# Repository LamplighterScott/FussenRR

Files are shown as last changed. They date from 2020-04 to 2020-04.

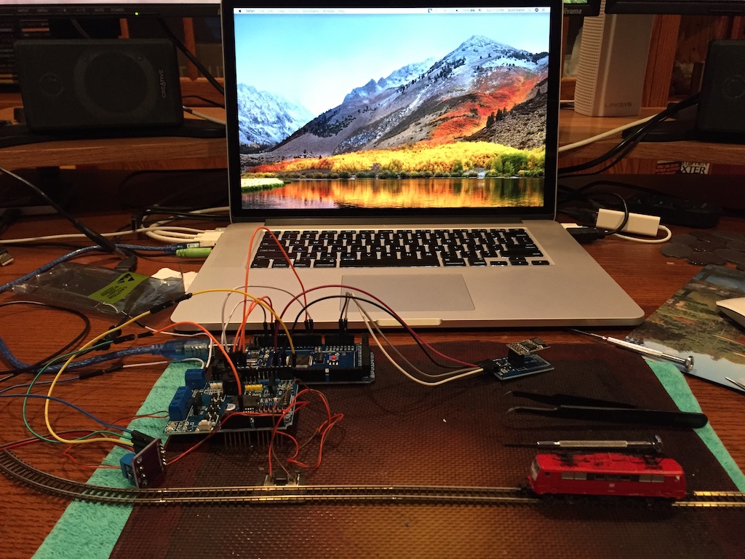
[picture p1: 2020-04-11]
IMG_0338 - Initial Testing.JPG

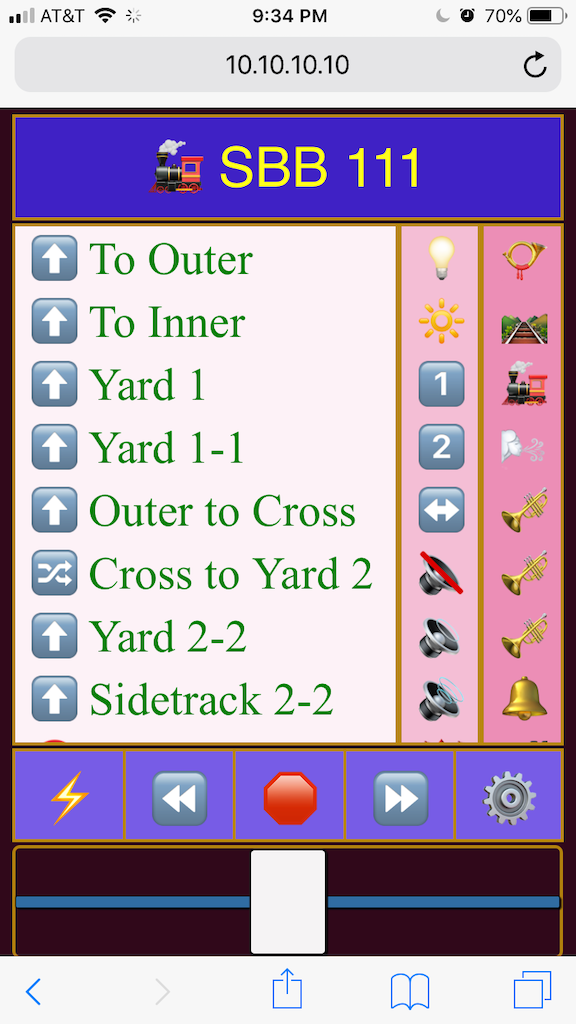
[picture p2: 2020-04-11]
IMG_1388 - Safari Controller.png

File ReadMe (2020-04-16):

FussenRR is a battery-operated Marklin Z model train set designed as a center piece for a dining room table.
It is completely controlled by a smart phone except for power on/off.  The name is taken from the train station
near Neuschwanstein castle in Germany.

It runs on a TalentCell Power Bank YB12011000-USB rechargeable battery (11,000 mAh), Geekcreit "Arduino Mega",
DeekRobot Motor Shield, Espressif ESP-01, Open-Smart ESP-01 Uart adapter, DF Player Mini, DSN-Mini-360 voltage
regulator (5v in 4.2v out), seven FLAMIN Robot 4 UO1 MOSFET relays, four TI 74HC595N shift registers.

The TalentCell lasts a long time inbetween charges.  It has three outputs.  The 12v output supplies the MOSFET
relays controlling eight turnouts (two solenoids each), four decouplers (one solenoid each) and one signal (two solenoids),
as well as some structure LED lights.  The 9v output supplies the motor shield for the DCC signal to the tracks and engines.
The 5v output supplies 1) the ESP-01/Adapter, 2) DF Mini Player/voltage regulator, 3) the shift
registers/turnout LEDs and 4) some LED structure lights.

The Motor Shield is piggy backed on the Mega and includes one jumper from pin 2 to 13 to configure it for DDC.
It is receives 12v from the battery.  It supplies power to the Mega and puts out the DCC signal to the main and
engine programming tracks.

The Mega operates on the 9v from the Motor Shield or five volts from the USB connection to a PC.
Serial zero is reserved for communication to a PC for script loading, debugging and engine programming via JMRI.
Serial one is for the DF Player.  Serial three is for the ESP-01.  Pinouts 2-13 (not all) are reserved for the Motor Shield.
Analog A0 and A1 pinouts measure the Motor Shield output amperage, allowing the Mega to disable the track power output
in case of a short on the tracks.  Turnouts, decouplers and signals are controlled by pinouts 22 to 49.  In order to
function as the DCC++ controller, talk to the ESP-01, DF Player, shirt registers and MOSFETs, you need to upload the
"DCCpp_Mega_MZ.ino" Arduino script to the Mega.  The upload speed is set in the script at 115,200 baud.  Make sure your
IDE (Arduino, ATOM, etc.) has the required library download to it from github, DFRobotDFPlayerMini).  The upload is carried
out on Serial Zero Tx0/Rx0 which can be accessed via the Mega's USB port from a PC.  The Mega has build-in USB to Uart
converter for this purpose.

The MOSFET circuits receive individual high signals from the Mega pin outs 22-49.  One MOSFET drives one solenoid.
Switching is via the negative outputs.  Positive is common.

The shift registers receive clock and data signals from three Mega pin outs (A13, A14, A15).  They drive all the turnout LEDs.
A series of resisters drop the voltage on the positive to each of the red and green LEDs so the brightness is
consistent between the two colors and the rest of the lighting on the set.  Switching is by the positve outputs.
Negative is common.

The DF Player is connected to the Mega's Serial One Tx1/Rx1 pins with a 1k ohm resister between the Mega's Tx1 pi
and the DF Player's Rx pin in order to drop the voltage from 5v to 3.3v.
The DF Player removable flash card is loaded with mp3 sound files.  Each MP3 file name must start with four digits.
The numbers should be in a continuous sequence: 0001xxx.mp3, 0002yyy.mp3 ... 0024zzz.mp3.
xxx, yyy and zzz can be any numberic or alphabet letters of any length; no spaces; dash or underscore are okay.

The ESP-01/adaptor is connected to the Mega's Serial Three Tx3/Rx3 pin outs.  The ESP-01 should be the 1mB size.
The ESP-01 communicates via WiFi to a smart phone using either WiThrottle for the Android or iPhone, or via a HTML
page tested on an iPhone and Safari.  The scripts for these two are different for the ESP-01.  The ESP-01 must be
removed from the set and plugged into a USB adapter for uploading scripts and/or data files from a PC.  For the
WiThrottle app, upload the script "WiThrottleOutputsVS.ino" to the ESP-01.   WiThrottle doesn't need any data files.
For the Safari version, you need to upload the script "FussenThrottle.ino" and the data files to the ESP-01.
The data files (FussenCSS.css, FusenHTML.html and FussenJS.js) need to be in a folder named "data".
For the Arduino IDE, the data folder needs to be at the same path level as the .ino file.  To upload the data files,
select "Tools" / "ESP8266 Sketch Data Upload".  For the ATOM IDE, the data folder needs to be at the path same level
as the "src" folder that incudes the .ino file.  For uploading the data files in ATOM, select "PlatformIO" / "Run other
target..." and then "PIO Uplaod File System image".  Upload speed is set in the script as 115,200 baud.  Make sure your
IDE has the required libraries downloaded to it (ESP8266WiFi, ESP8266mDNS, ESP8266WebServer, FS, DNSServer, WebSocketServer)

The URL is set in the script as "10.10.10.10" without a password.  To use either one, you need to switch your smartPhone to
the "FussenRR" WiFi server in Settings.  Your smartPhone will seek your normal WiFi server after the train set power is
turned off.  The name can be changed in the ESP-01 script.  For WiThrottle, you need to download the app and then enter
the URL (10.10.10.10).  For the HTML version, you only need to enter 10.10.10.10 in the Safari search field.   

Two types of engine decoders are employed, VELMO and DigiTrax.  The DigiTrax (DZ123MO for Z 88584 and DZ123MK1) boards
provide speed and direction control for the engines and the id is resettable.  However, I cannot enable the basic
functionality, such as, light on/off and shunting using DCC++ through JMRI.  The VELMO (LDS26306 for BR111 and LDS22331
for BR103) boards fit the two of the other engines I have which are not supported by DigiTrax.  The default functions
all work well.  However, I have not figured how to change the VELMO id and set-up with DCC++ and JMRI.  My other
challenge is to adapt a Marklin 81360 snow plow set to DCC.

Development notes:

The turnouts were first operated by Darlington relays (ULN2803APG) - what you see in the early photos with bread boards.
These worked fine in testing and for the turnouts near (<30cm) to the relays.  However, the output was too weak for the
turnouts at the far end of the layout which are almost a meter away.  The voltage drop of about 3-4v from the Darlingtons
was too great.  The wiring is small (24-26ga) running close in parallel. The Marklin turnouts are desigend to be supplied
with 10v AC from the Marklin power supply.  As we know, the voltage drop for AC over a distance is lower than DC.
Furthermore, running 12v DC imparts less umpf to the solenoids than 10v AC.

As a solution, I considered making my own MOSFET relay cirucit board, employing several FLAMIN Robot 4 UO1 MOSFET boards
or the 32 MOSFET array solution from Cross Roads Fencing Center (http://crossroadsfencing.com/BobuinoRev17/index.html).
MOSFETs have a much smaller voltage drop than Darlingtons.  I tried one FLAMIN board and it worked, although I had to
bipass one of the photocouplers - you get what you pay for.  They connect to the Mega invididual output pins via a
photocoupler so the 12V is electrically isolated from the Mega 5v output pins.  They take up a little more room than
the Cross Roads board.  The Cross Roads board would connect to the Mega via shift registers.  This would require way
fewer connections (3 signal connections for 32 relays vs 32 pinout connections for the equivalent number of relays using
the FLAMIN boards) and the board could be connected in series to the turnout signal light LED shift registers.  If I was
starting from scratch, I would go with the Cross Roads solution.  The Mega script would have to be modified, as well.
Furthermore, the DF Player and ESP-01 communication could be converted to SoftSerial and the Mega reduced to an Uno or
possibly something even smaller, if a smaller motor shield could be found that runs DCC adequately - not all motor
shields work for DCC++.

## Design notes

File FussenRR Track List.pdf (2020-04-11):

Rail Tracks list

Layout Name: A_Marklin Z - Final 2

Dimensions: 1,510 x 594.9 mm 14,462.7 mm

Rail Tracks list: Märklin Z v.1.1
8500 | Straight | 17
8503 | Straight | 2
8504 | Straight | 7
8505 | Straight | 20
8506 | Straight | 3
8510 | Curve | 16
8520 | Curve | 4
8521 | Curve | 8
8530 | Curve | 6
8531 | Curve | 5
8560 | Single slip | 1
8562-8565 | Turnout left | 1
8563-8566 | Turnout_right | 3
8568 | Curved turnout left | 2
8569 | Curved turnout right | 1
8587 | Straight | 4
8588 | Straight | 4
8590 | Straight | 1
8591 | Curve | 4

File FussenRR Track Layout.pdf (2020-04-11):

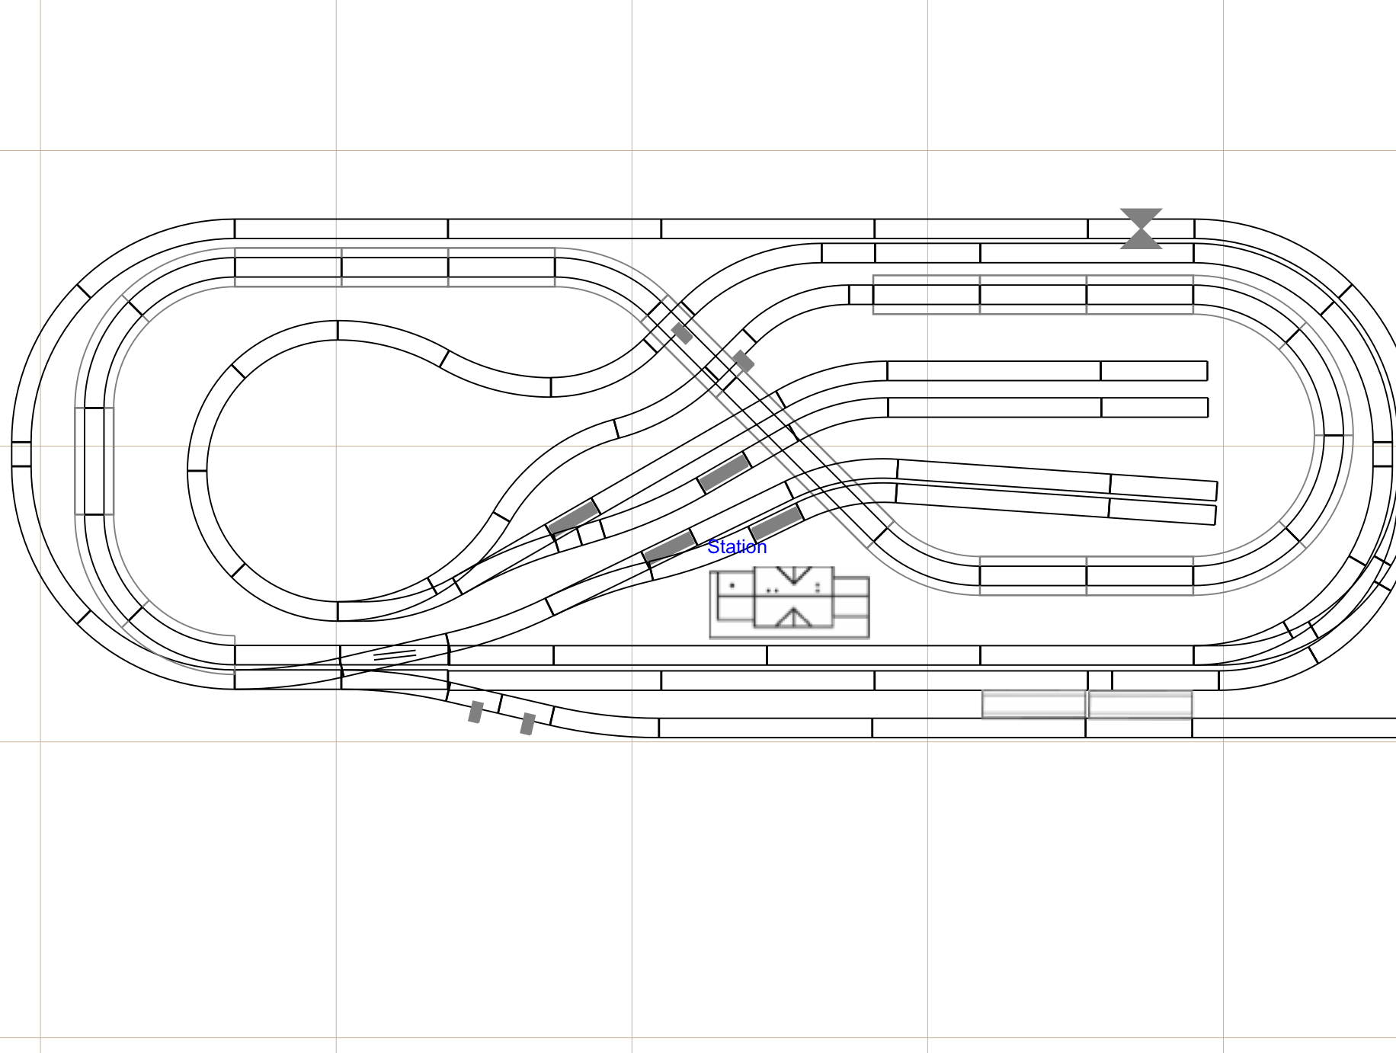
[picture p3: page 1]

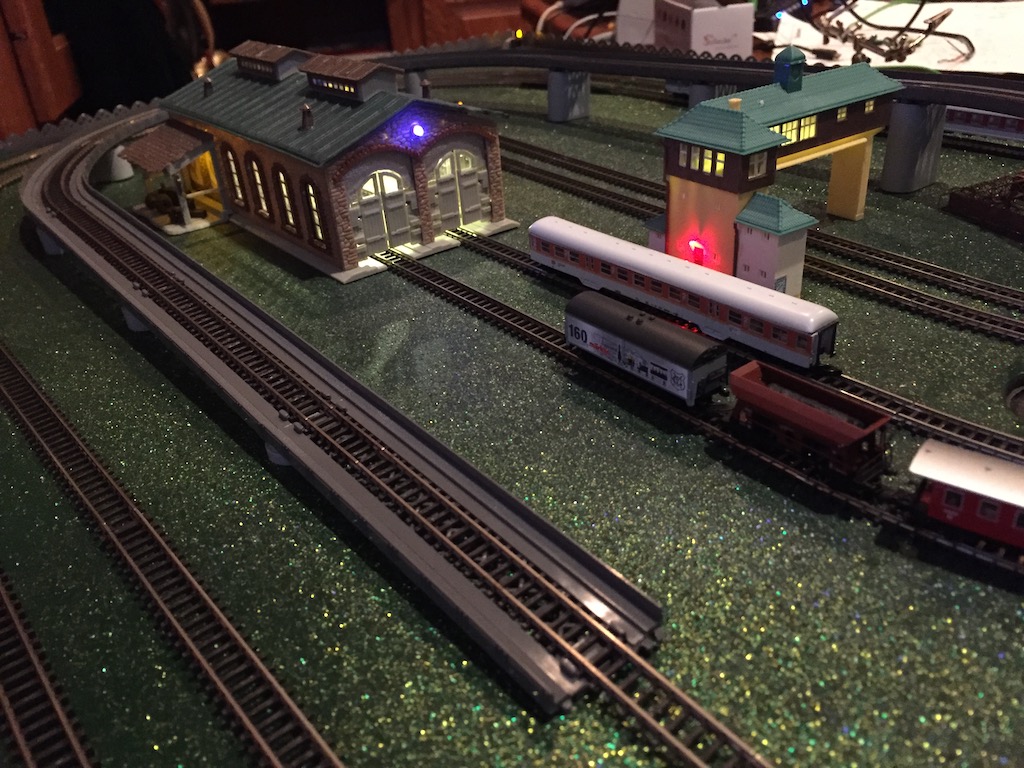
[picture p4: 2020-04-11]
IMG_1040 - Train Barn.JPG

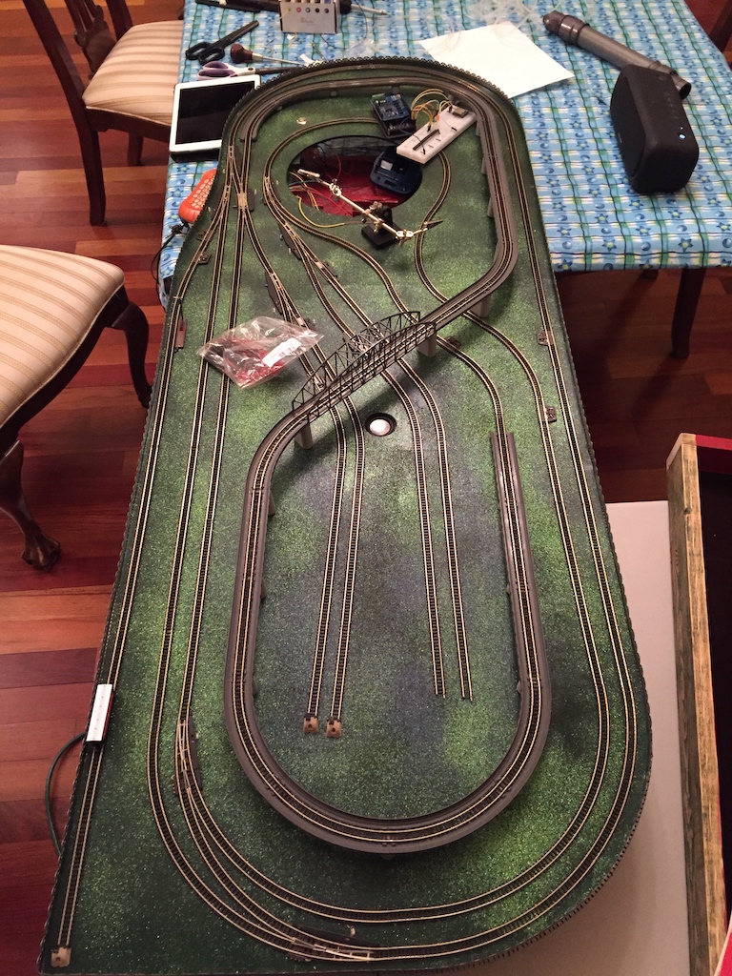
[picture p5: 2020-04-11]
IMG_0694 - Track Layout.jpg

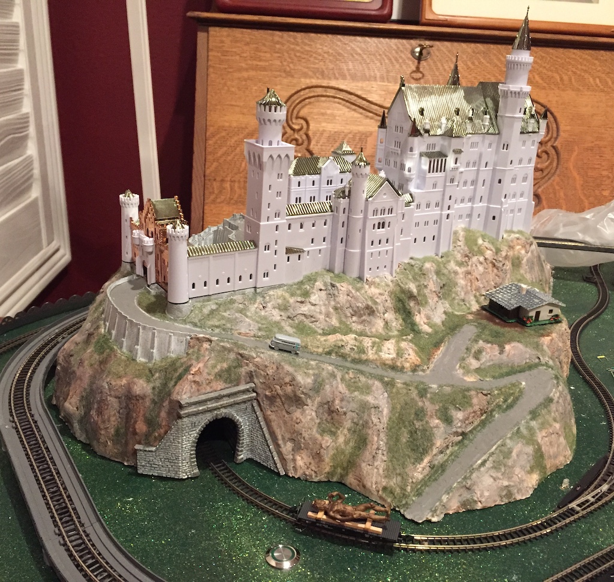
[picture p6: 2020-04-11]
IMG_1320 - Neuschwanstein.jpeg

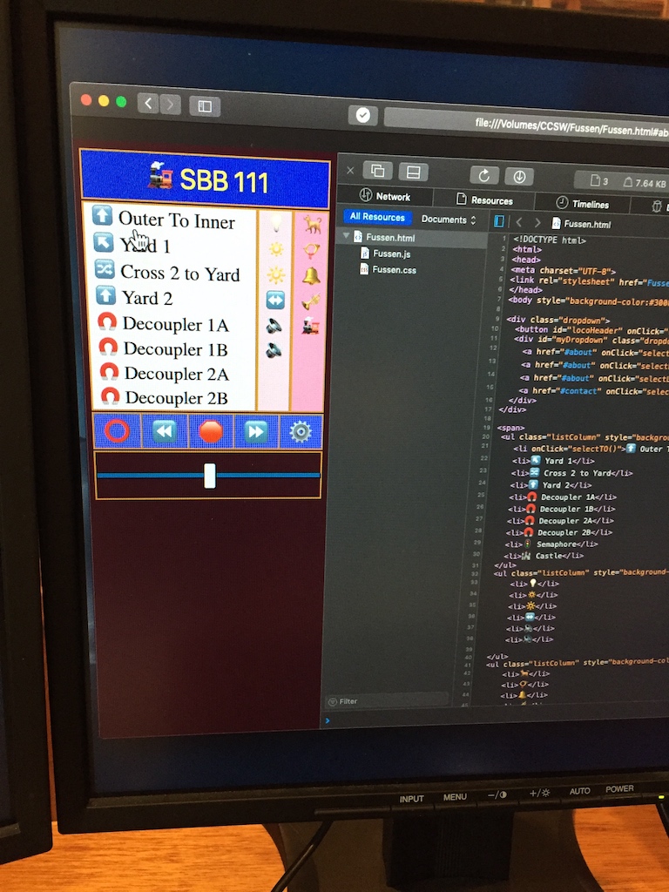
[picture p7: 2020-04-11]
IMG_1034 - Safari Controller dev.jpg
